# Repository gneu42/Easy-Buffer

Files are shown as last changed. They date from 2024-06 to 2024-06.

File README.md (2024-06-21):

<h1 align="center"><ins>Easy-Buffer</ins></h1>

<H2 align="center">ERCF Buffer with assisted loading function for ERCF V2.</H1>

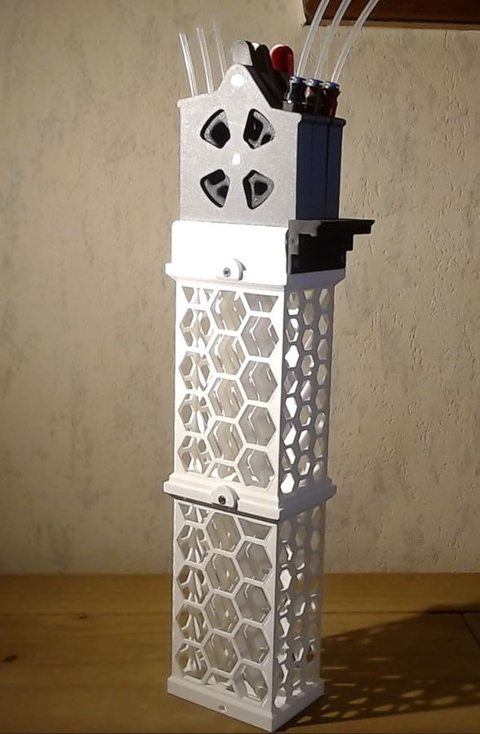
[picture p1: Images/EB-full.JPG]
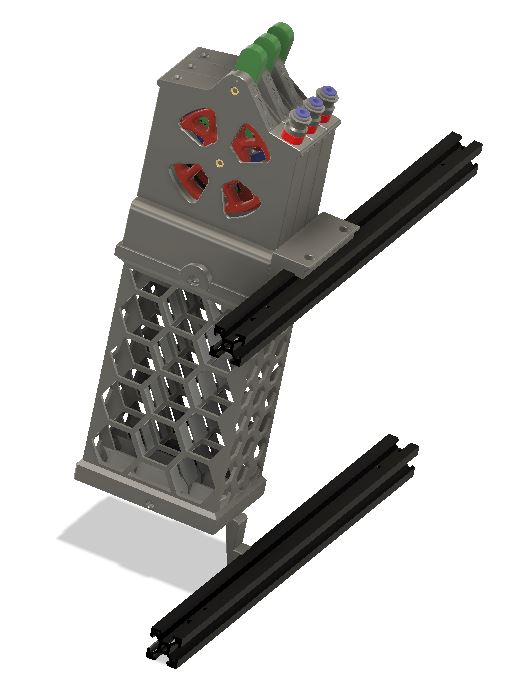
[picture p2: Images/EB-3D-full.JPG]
<p align=center></P>

## What is it ?

**Easy-Buffer** is based on single loop buffer like Quiver or the Prusa MMU2 Filament Retract Bank. It can be associated to the ERCT-lite, for people that can't use the official Cotton Tail (ERCT)

The bottom clamp is designed to hold 3 buffer towers on a Voron 2.4 350. For other printer, the clamp should be redesigned.
Using 3 Buffer Towers, it will be possible to buffer **1000mm** of filament. 

It consists of :
  * 150mm high stackable buffer towers.
  * An interface block.
  * 3 individual heads.
        The heads are composed of :
        * a case with cover.
        * a wheel.
        * a filament guide.
        * a lever.
        * an magnetic PTFE output.

Using the pre-gate function of Happy Hare, the loading of the filament in the ERCF takes only a few seconds from the insertion into the buffer to the parking in the filament block.

To load the filament, simply move the lever to the **L** position, and insert the filament until it reaches the ERCF gate. Happy Hare will pull it and push it back to the parking position. At this moment, filp the lever to the **B** position. That's it. It is ready for printing.

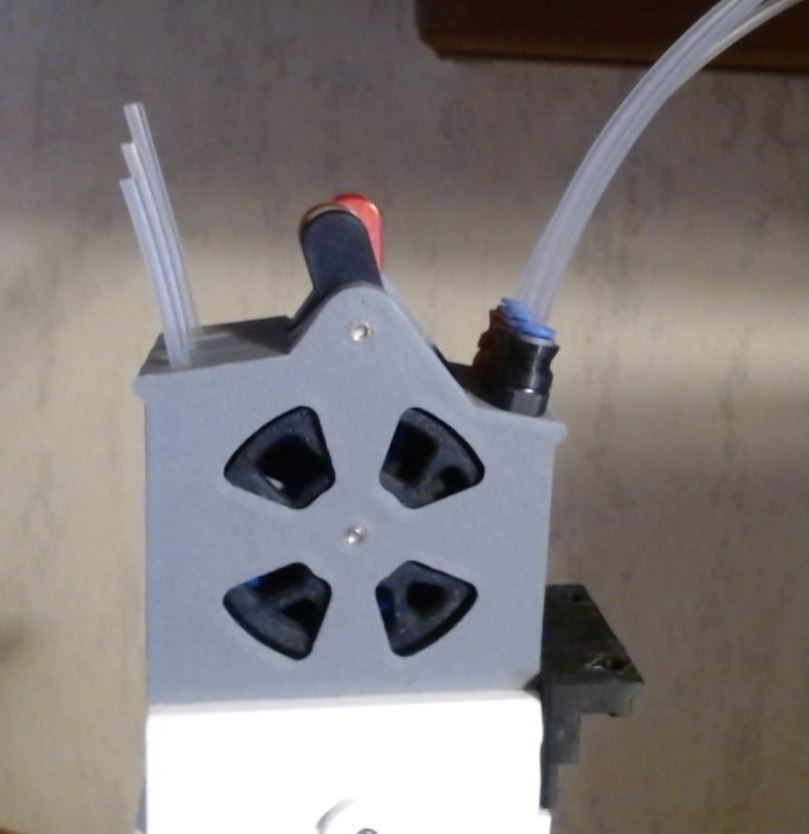
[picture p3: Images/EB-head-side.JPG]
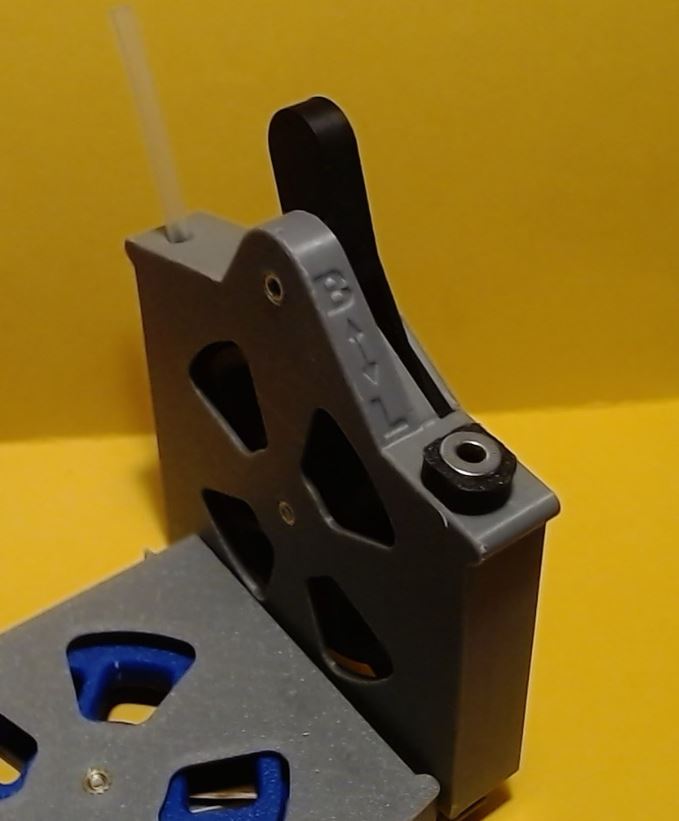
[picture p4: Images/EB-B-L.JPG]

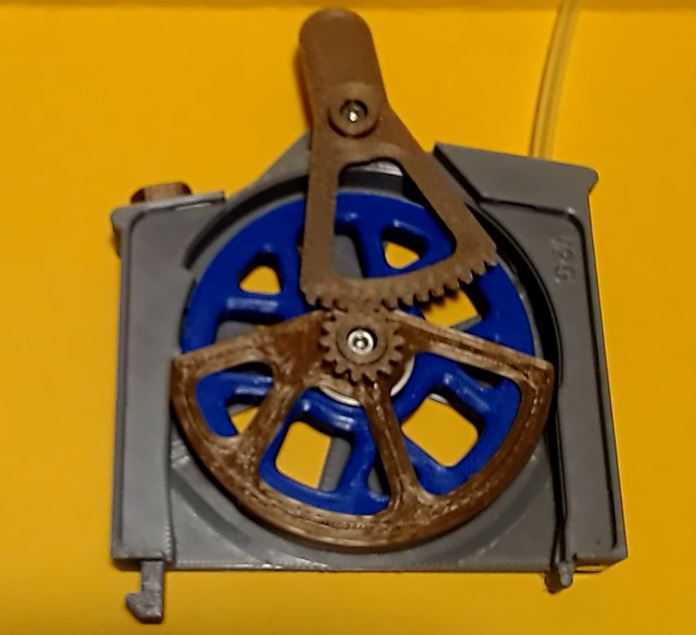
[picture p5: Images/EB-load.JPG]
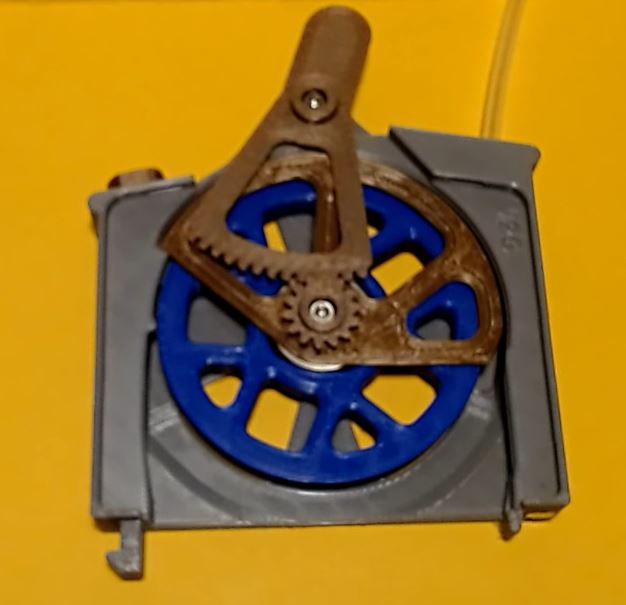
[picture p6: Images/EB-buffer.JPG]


## Summary.
* **[Bom](#bom)**
* **[Printing tips](#printing-tips)**   
* **[Cleaning tips](#cleaning-tips)**
* **[Assembling tips](#assembling-tips)**
* **[How to use it](#how-to-use-it)**

## BOM.
For each buffer head you need :  
   * 2 M3x12 SHSC screws. 
   * 2 M3 inserts.
   * 1 6x3 magnets.
   * 2 10x4x4 magnets (with 4mm hole).
   * 1 ECAS (on the filament path).
   * 1 optional sprint 3.7x7 spring (0.5mm wire). 
   * 1 optional 4mm ball.
   * 1 608ZZ bearing

For each buffer tower you need :
   * 2 M3 inserts.
   * 2 M3x6 SHSC screws. 

For each interface plate you need :
   * 6 M3 inserts.
   * 2 M3x6 SHSC screws. 
   
For the 2020 mounting plate yu need :
   * 6 M3 hammer nuts
   * 2 M3x8 SHCS

For the bottom clamp (only for Voron V2-350)
   * 1 M3x12 SHCS
   * 1 M3 Hammer nuts

## **Printing tips:**
   * I have printed the parts in PLA with the following settings :
     * 4 perimeters.
     * 3 top and bottom layers.
     * 25% infill.

   * Since the lever gear is quite thin, I advice to print at least one spare lever. With all the tests I've made, I never had one that failed, but we never know. Only time will tell. 

## **Cleaning-tips:**
   * Remove all supports. (see assembly instructions)
     * The big support on the guide can easily be removed with a spatula used to remove print off of the bed. Insert it at easiest point, and work your way around until it is completely free from the guide.

   * The tolerances are quite tight, depending on your printer, you may need to clean the guide and lever holes, so they turn freely.

   * Remove the "elephant foot" especially on the lever gear.

   * To get a smoother flip of the lever after the filament has been loaded, you should smooth out the layer steps on the guide with a file or sand paper.  You can also spray a bit of dry lubricant on those areas.

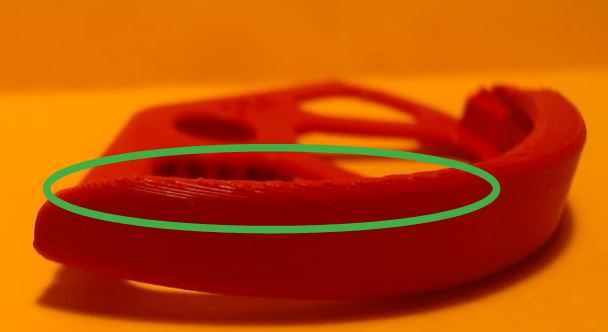
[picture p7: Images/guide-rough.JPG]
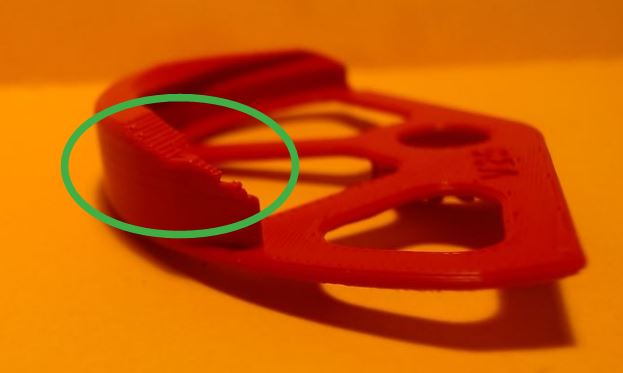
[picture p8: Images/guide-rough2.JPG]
   

## **Assembling-tips:**

   * The provided Bottom Clamp is designed to hold a 3 Buffer towers on a Voron 2.4-350mm. 
   * Insert a short PTFE tube into the 4mm hole on the top of the Head. This is the entry side.
   * Insert an ECAS or the provided magnet holder into the hole at the other side of the head. The magnet holder is a bayonet type.

   * [Assembly instructions.pdf](Assembly_instructions.pdf)

## **How to use it:**
The Easy Buffer Head has 2 functions 
   1. Load the filament easily into the ERCF. It is even easier if you use the pre-gates switched of Happy Hare that will park the filament into the filament block for you.
   2. Allow the filament to go down into the buffer towers.
    
* **Loading the filament**  
  It is recommended to insert the filament into the head with the natural curve of the filament following the wheel.
  1. Flip the lever to the "L" position.
  2. Insert the filament into to small PTFE tube at the entry side until it comes out on the exit side. From there you can either:
     1. leave it there to insert it later into ERCF
     2. keep pushing on the entry side until it get into the ERCF, and if you have pre-gates sensors, Happy Hare will pull it and park it in the filament block.
  3. Once the filament is loaded or at least out of the head at the exit side. Flip the lever to the "B" position. This will move the guide over the filament, and make the system ready for buffering the filament. *It is best to move the lever in a **single fast move** otherwise it could stop in the middle of its travel.*

Once the lever is on the "B" position, it will not be possible to move it to the "L" position until the filament is completely removed.

  * **What the lever does not move fully to the "B" position**
      The whole system relies on the guide sliding over the filament. To do this, the guide must also bend the filament slightly over a short length. Depending on the type and smoothness of your filament, it is possible that the guide has problem to slide over or bend the filament.
      In that case, pushing a bit the filament coming from the spool into the head to release pressure will normally allow the lever to go to the "B" position.  

  * If all is working well, it is possible to load 10 filaments in 3 minutes.
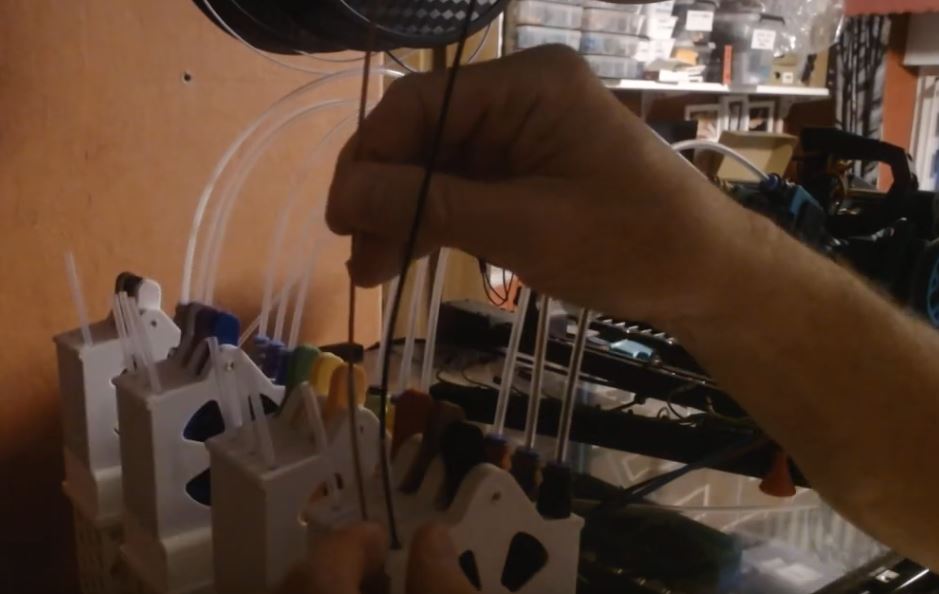
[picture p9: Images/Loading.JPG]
Loading
<p align=center>

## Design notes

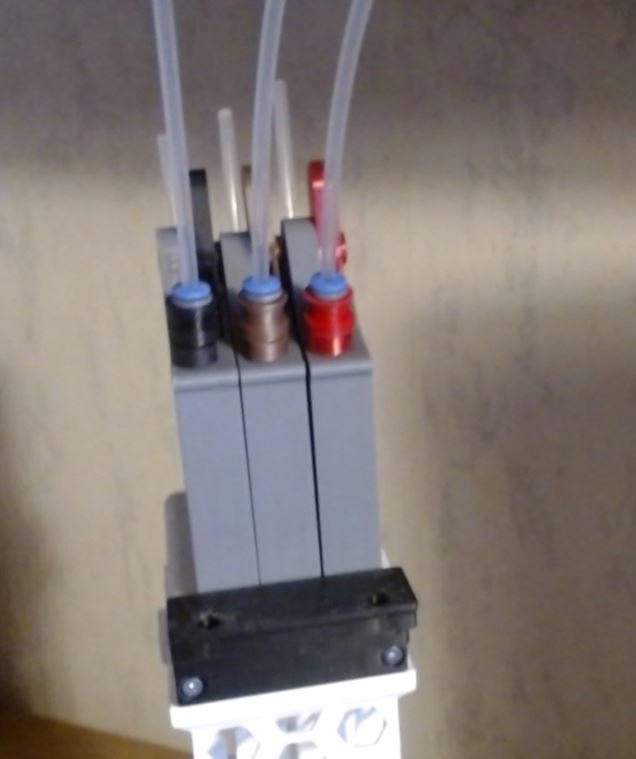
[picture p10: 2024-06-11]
Images/EB-head-out.JPG

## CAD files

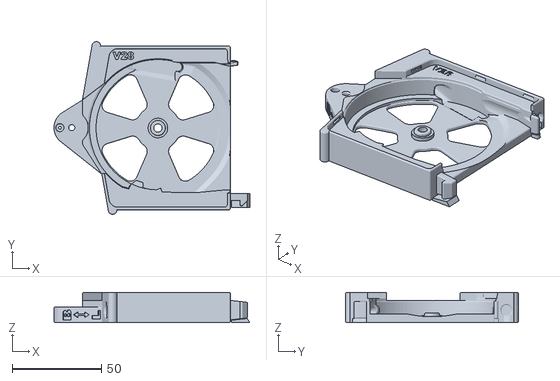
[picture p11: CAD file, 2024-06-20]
STL/Buffer_Head_case.stl
109.7 x 96.7 x 17.0

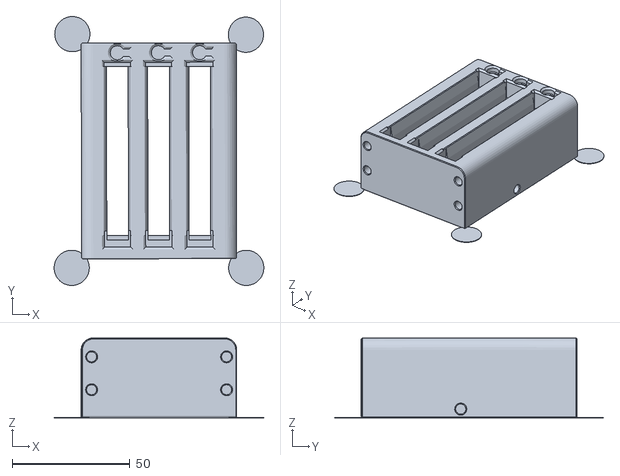
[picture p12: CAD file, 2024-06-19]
STL/Interface_block.stl
89.2 x 114.4 x 34.0

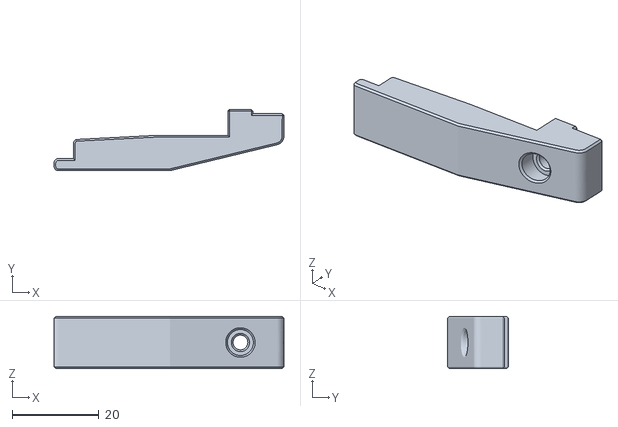
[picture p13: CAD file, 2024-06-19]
STL/Bottom_clamp_V2-350.stl
53.0 x 14.2 x 12.0

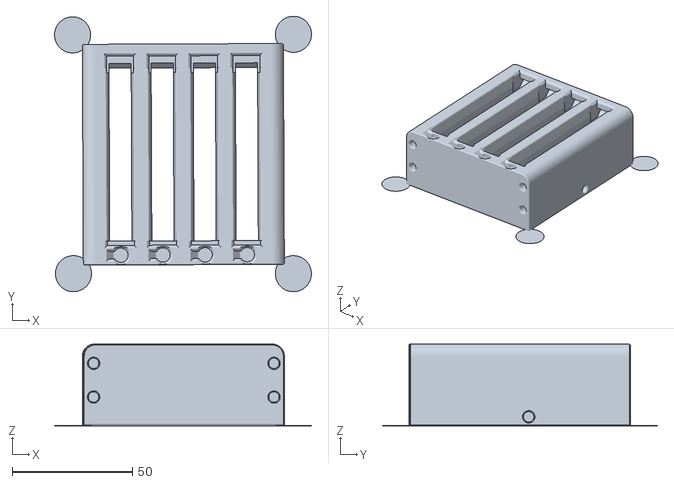
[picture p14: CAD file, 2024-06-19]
STL/Interface_block_4_Channels.stl
106.7 x 114.4 x 34.0

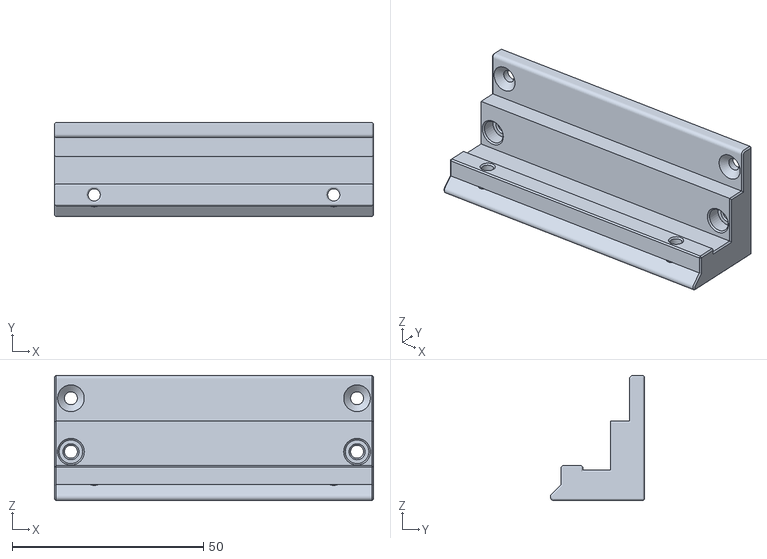
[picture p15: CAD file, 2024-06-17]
STL/20x20-holder_4_channels.stl
83.5 x 24.7 x 32.8

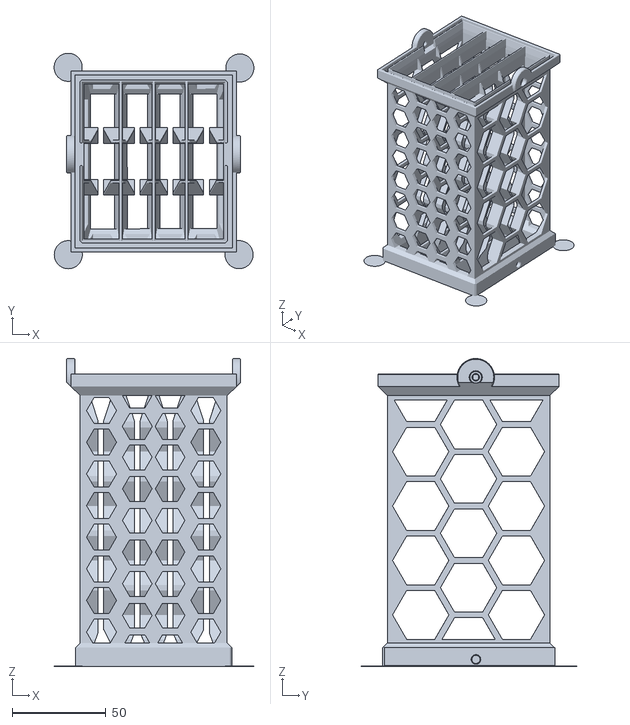
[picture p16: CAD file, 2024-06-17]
STL/Buffer_tower_4channels.stl
106.4 x 114.8 x 164.1

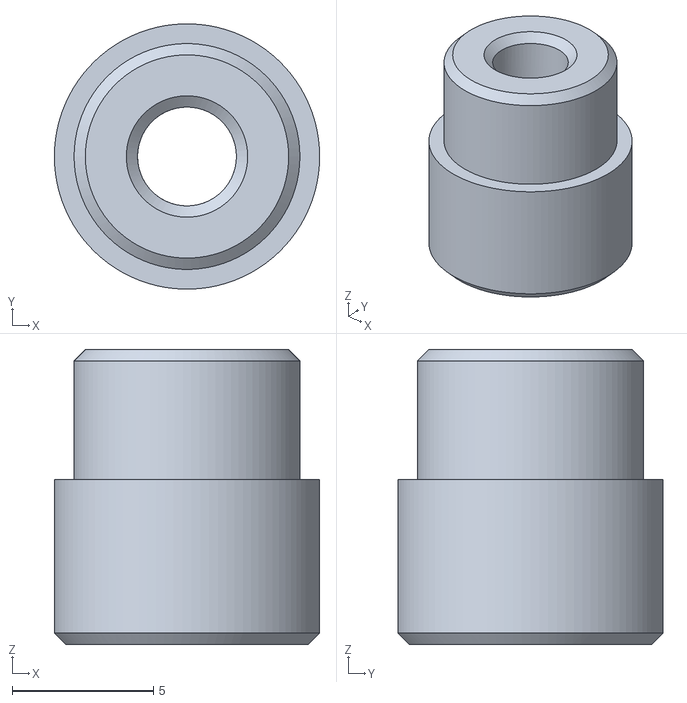
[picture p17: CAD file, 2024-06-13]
STL/Wheel_hub.stl
9.40 x 9.39 x 10.4

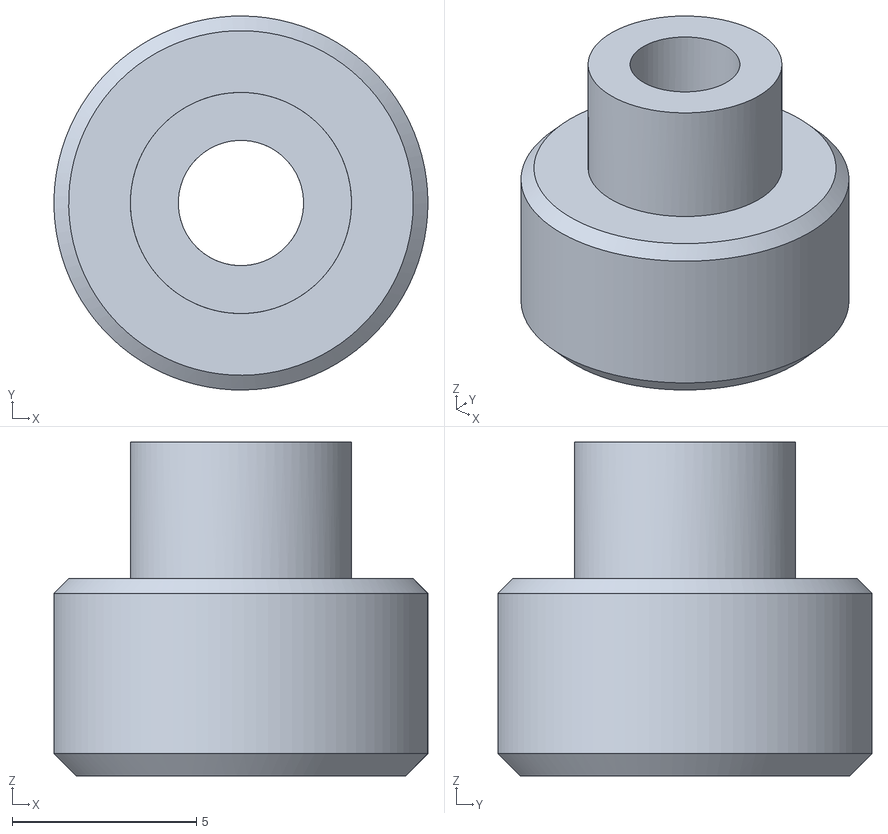
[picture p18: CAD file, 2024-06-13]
STL/Lever_hub.stl
10.1 x 10.1 x 9.05

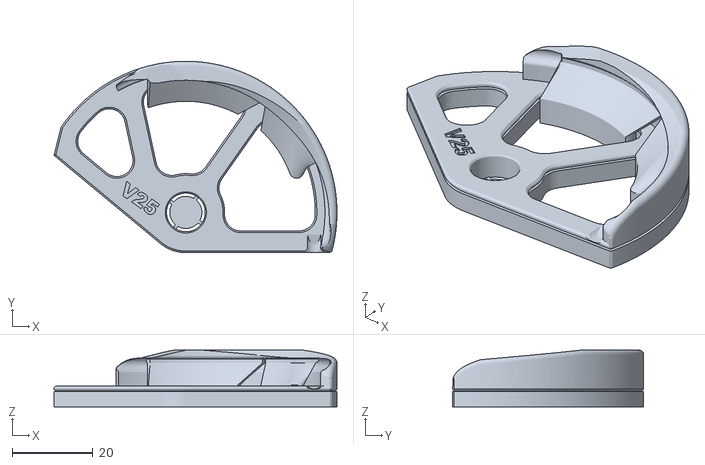
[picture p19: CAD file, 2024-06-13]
STL/[a]Filament_guide.stl
70.2 x 47.5 x 14.1

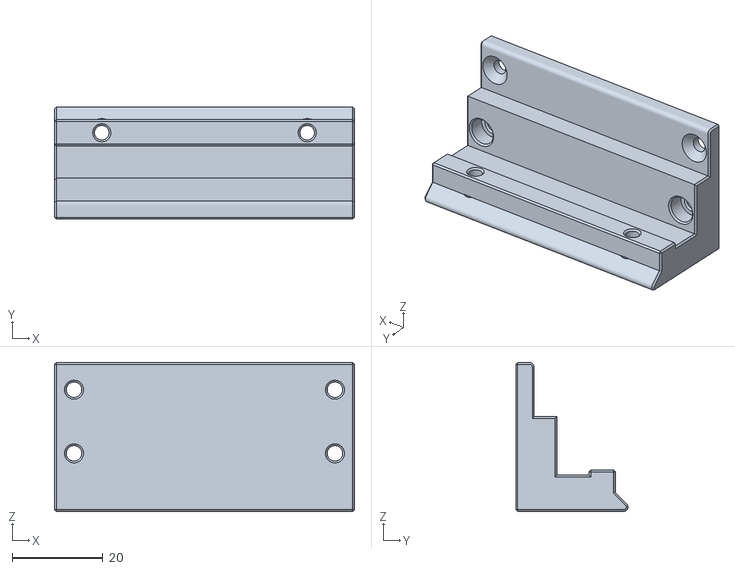
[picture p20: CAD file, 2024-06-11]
STL/20x20-holder.stl
66.0 x 24.7 x 32.8

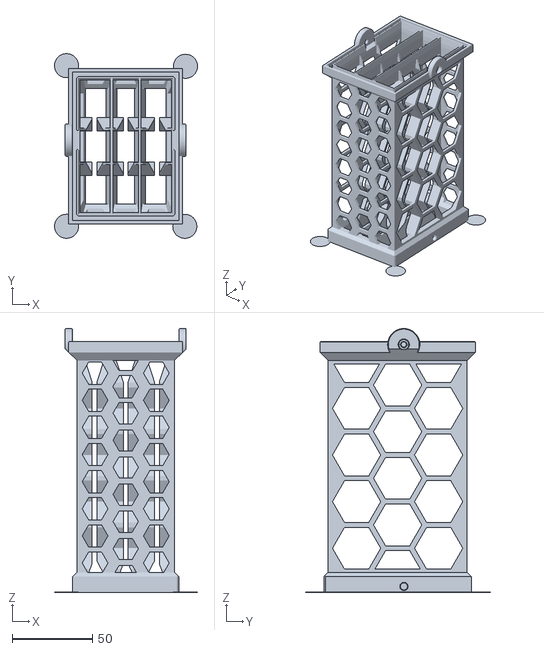
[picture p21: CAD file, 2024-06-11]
STL/Buffer_tower.stl
88.9 x 114.8 x 164.1

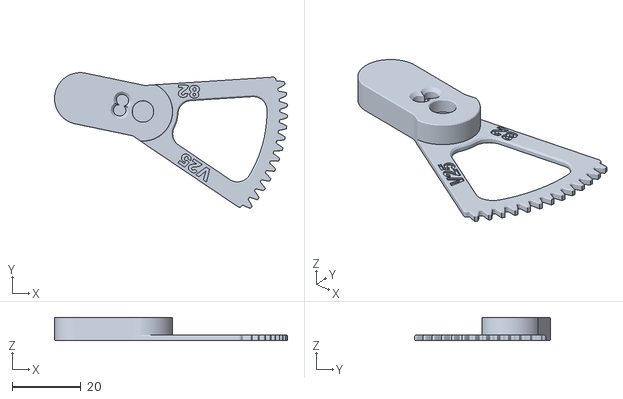
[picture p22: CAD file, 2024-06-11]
STL/[a]Buffer_Lever.stl
67.5 x 39.3 x 6.80

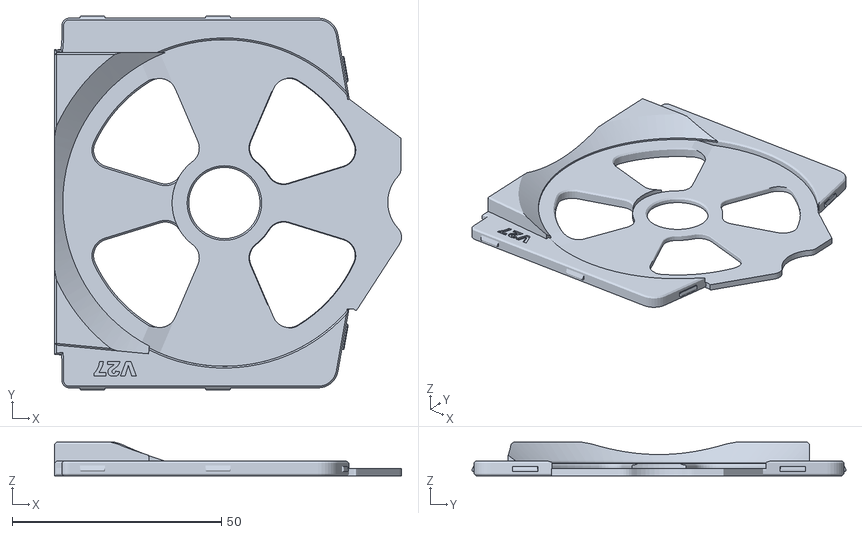
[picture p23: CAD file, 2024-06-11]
STL/Buffer_Head_Cover.stl
82.9 x 89.3 x 8.00

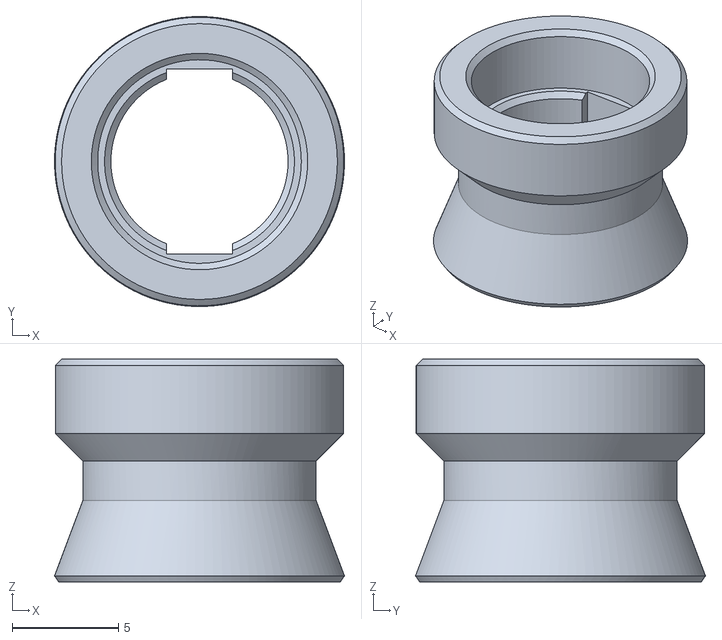
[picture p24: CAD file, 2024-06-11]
STL/ECAS_9.6mm_Magnet.stl
13.7 x 13.7 x 10.5

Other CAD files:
STL/PTFE_Bayonnette_Entry_10mm_Magnet.stl
STL/ECAS_10mm_Magnet.stl
STL/PTFE_Bayonnette_Entry_9.6mm_Magnet.stl
STL/[a]Buffer_Wheel.stl

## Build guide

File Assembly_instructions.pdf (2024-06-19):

# Assembly instructions

## Supports removal

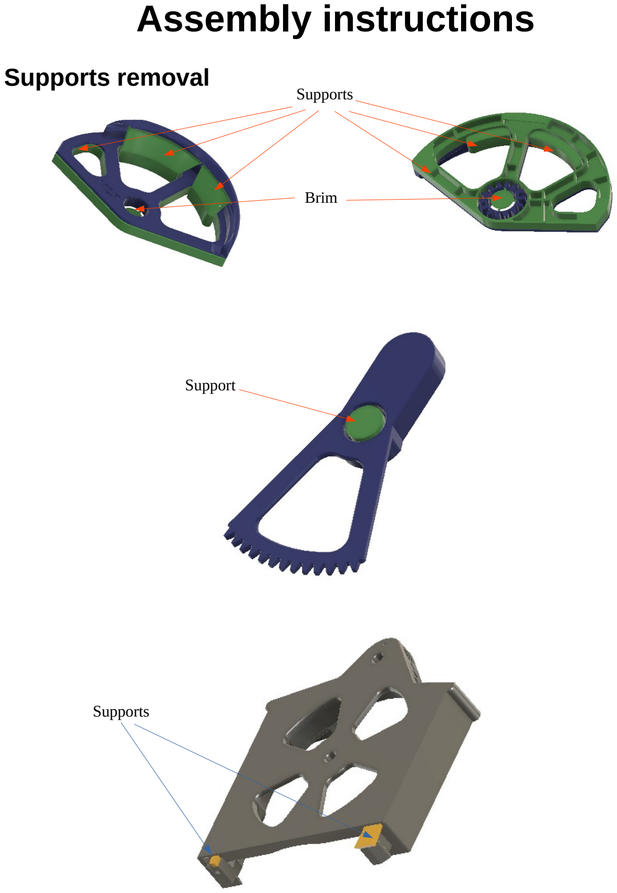
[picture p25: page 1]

Supports

Brim

Support

Supports

M3 Inserts.

Buffer tower

Interface block

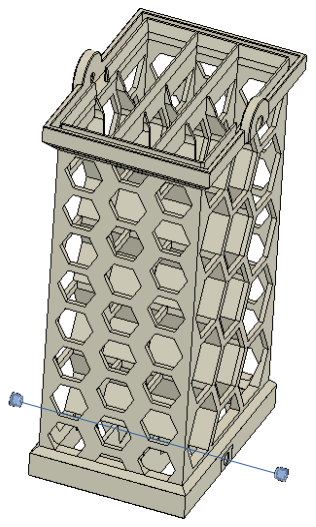
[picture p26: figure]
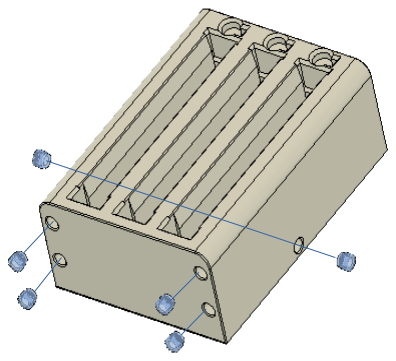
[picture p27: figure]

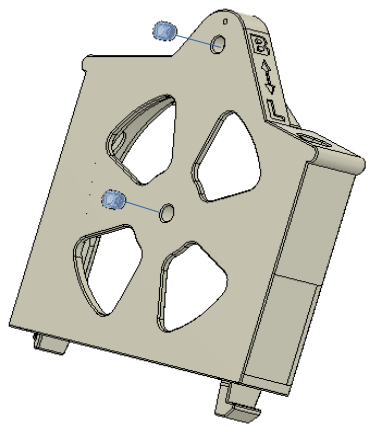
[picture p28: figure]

Case

## 6x3 Magnets

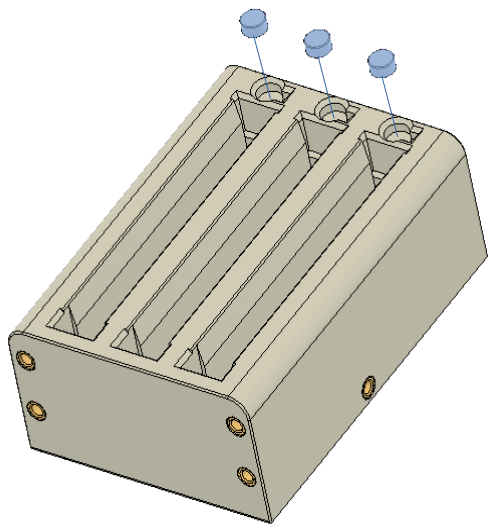
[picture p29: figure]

Interface block

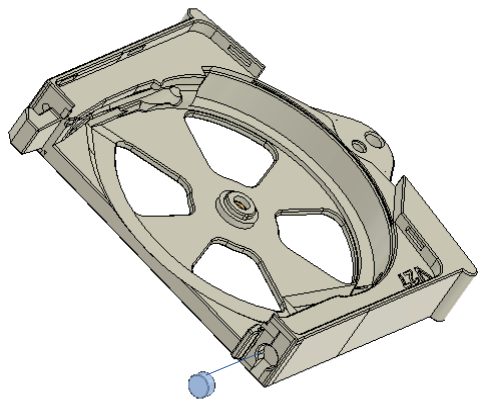
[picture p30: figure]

Case

Assembling the parts.

The buffer tower stack.

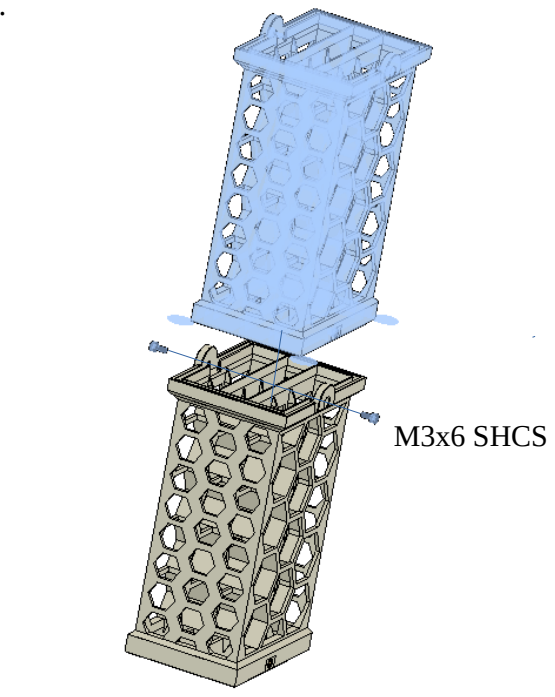
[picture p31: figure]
M3x6 SHCS

Use as many tower as you need.

Assembling the interface block to the Buffer tower

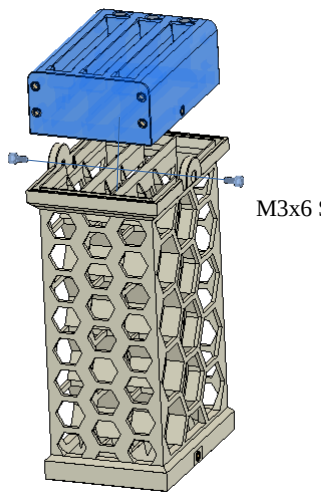
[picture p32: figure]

M3x6 SHCS

## Assembling the buffer Head

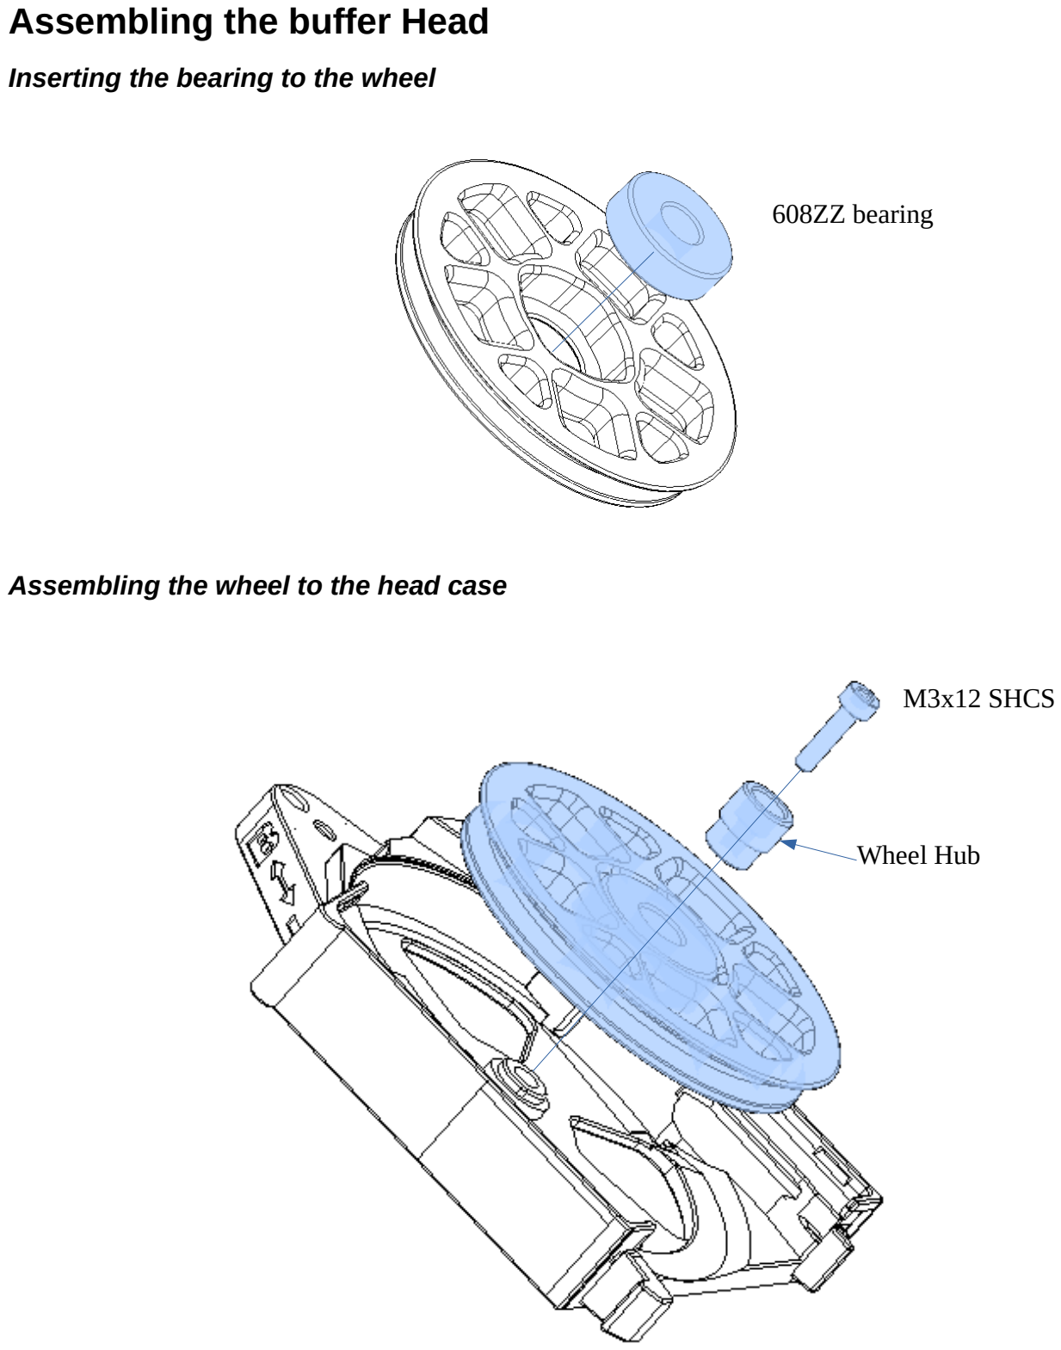
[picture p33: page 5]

Inserting the bearing to the wheel

Assembling the wheel to the head case

608ZZ bearing

M3x12 SHCS

Wheel Hub

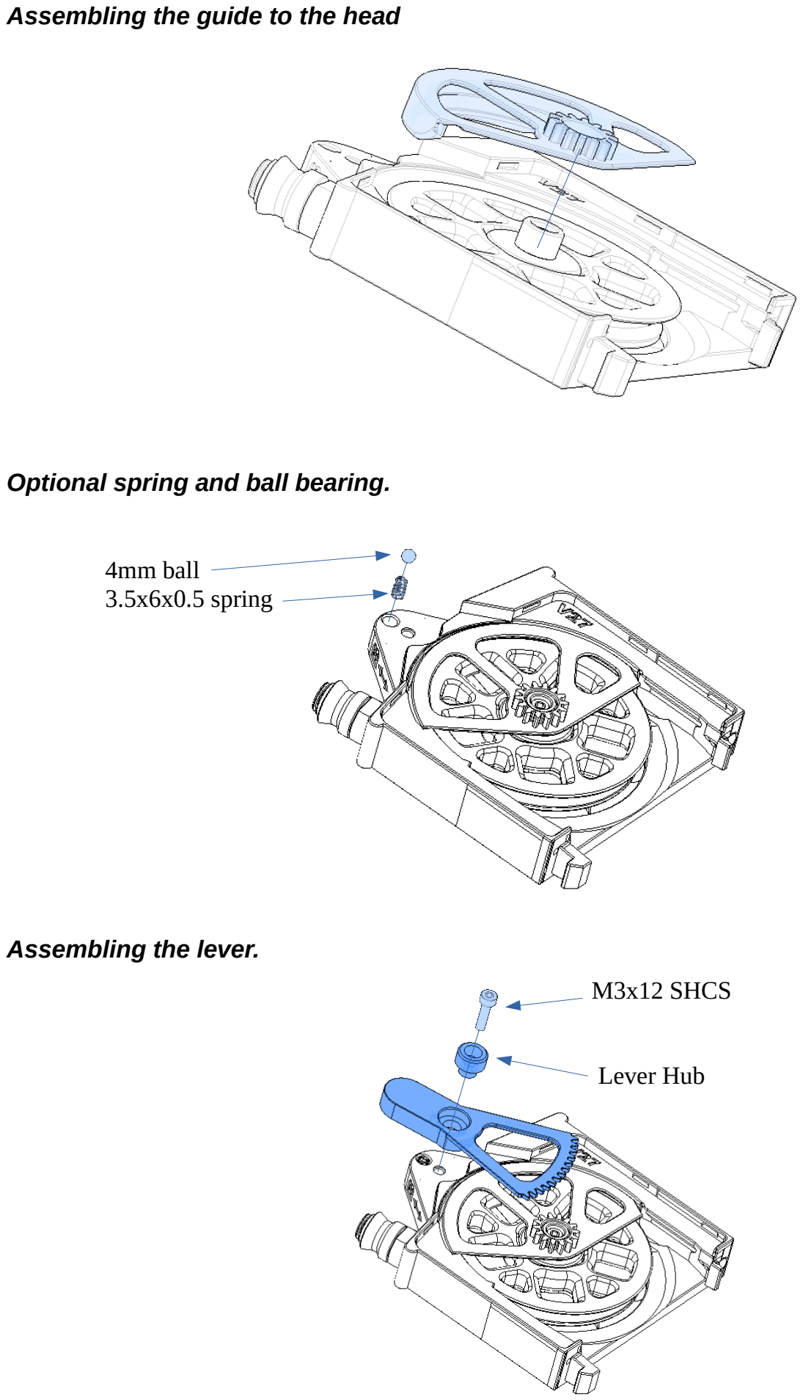
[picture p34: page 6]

Assembling the guide to the head

Optional spring and ball bearing.

Assembling the lever.

4mm ball
3.5x6x0.5 spring

M3x12 SHCS

Lever Hub

Adjusting the gear.

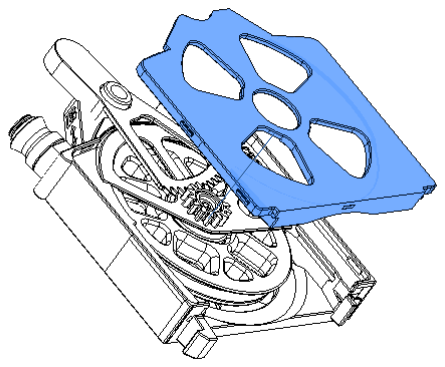
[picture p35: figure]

Closing the head

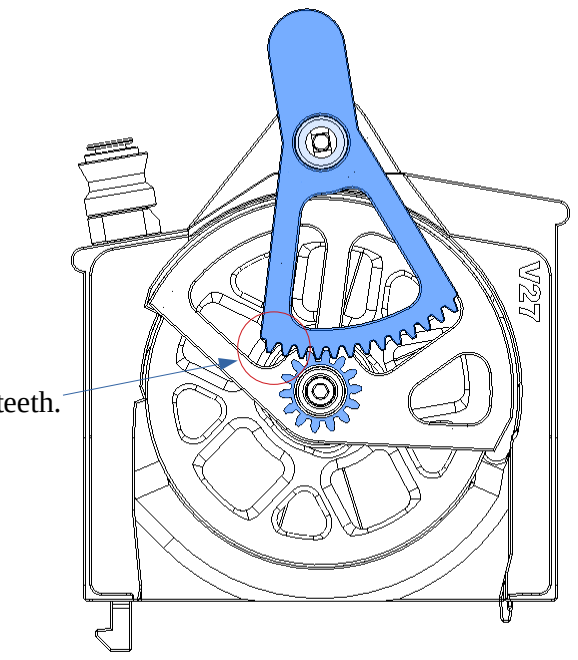
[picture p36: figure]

2 free teeth.

Installing the head on the interface block.

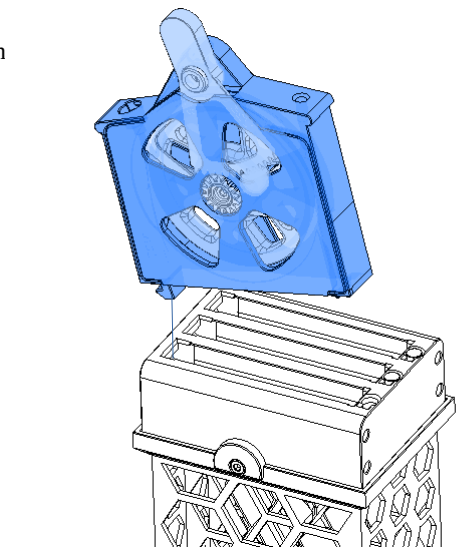
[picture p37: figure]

Insert the hook first, then
tilt the head so the
magnets stick together.

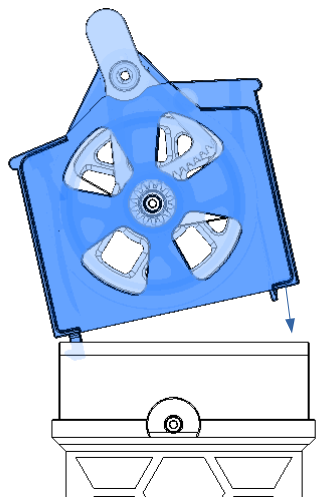
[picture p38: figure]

## Usage

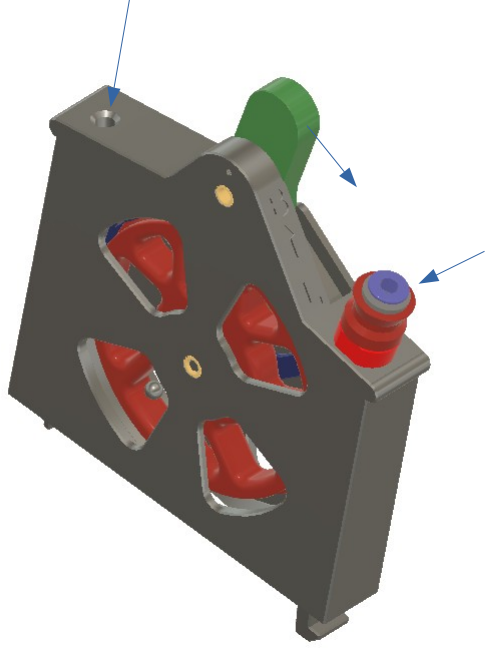
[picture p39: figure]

Filament loading
position

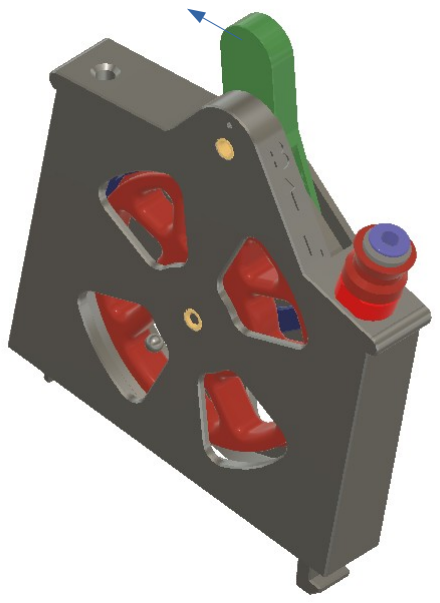
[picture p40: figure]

Printing / buffering
position

Output to ERCF

Input from spool

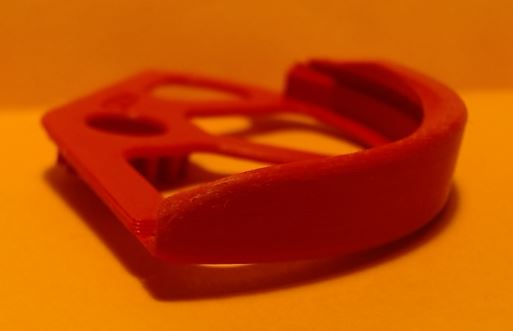
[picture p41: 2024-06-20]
Images/guide-smooth.JPG

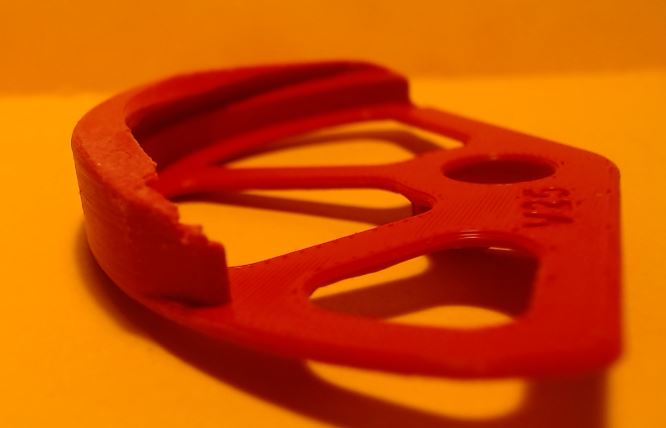
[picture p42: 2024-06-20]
Images/guide-smooth2.JPG

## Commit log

2024-06-11 Add more STLs
    [20x20-holder.stl, Bottom_clamp.stl, Buffer_tower.stl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]
2024-06-13 Update STL
    [Lever_hub.stl, Wheel_hub.stl, [a]Filament_guide.stl]
2024-06-14 Add assembling instructions
2024-06-17 Update Assembly instructions.pdf
2024-06-17 add 4 channels STL
    [20x20-holder_4_channels.stl, Buffer_tower_4channels.stl, Interface_block_4_Channels.stl]
2024-06-19 Update STL and readme.
    [Bottom_clamp.stl, Bottom_clamp_V2-350.stl, Interface_block.stl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]
2024-06-20 Update head case STL and add more info in readme.
    [Buffer_Head_case.stl]
2024-06-20 Fix assembly instruction link
2024-06-20 Correct BOM on readme.md
